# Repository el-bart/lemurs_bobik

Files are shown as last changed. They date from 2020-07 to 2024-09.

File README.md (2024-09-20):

# Lemur's Bobik

project of a toy for a 3-5 year child, that is aimed at learning basic programming skills.
robot has 4 buttons for programming directions and one button to start it.

program is generated by a sequence of buttons pressed (eg. forward, forward, left).
after pressing "start" button, robot begins execution of a given sequence.
its programming is thus similar to Logo programming language, but does not require one to be able to read/write, or spending time in front of the screen.

robot's body is designed to mimic a bit autonomous vacuum cleaner robots, that children know and love. :)

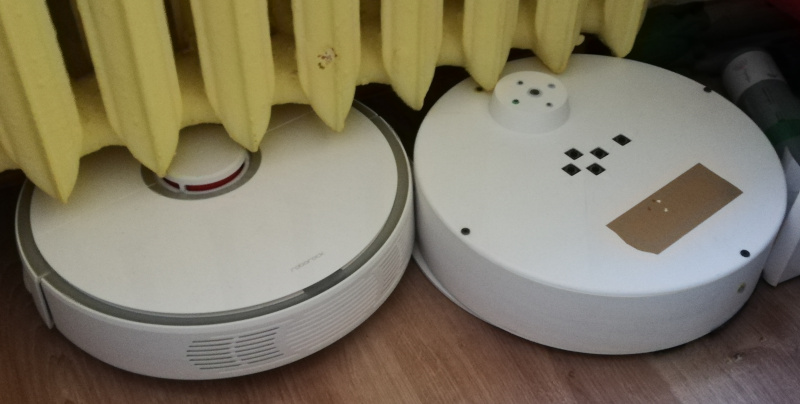
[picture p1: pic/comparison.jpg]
comparison of toy and real robot


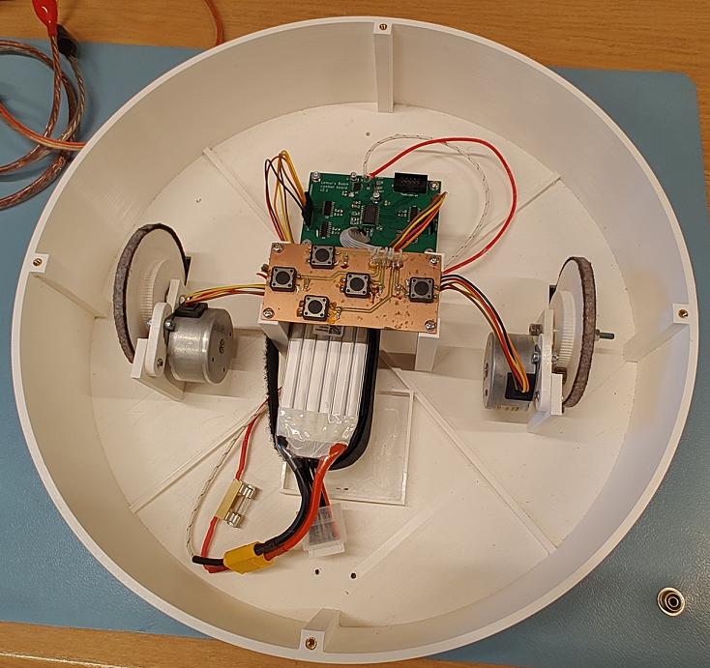
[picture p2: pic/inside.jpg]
robot's interior


## HW parts

* 2x unipolar stepper motors (M42SP-5M - from old desktop printer)
* 12x M3x10 screws
* 12x M3 threaded inserts
* velcro for holding LiPo pack in place (length according to your LiPo size)

## 3D printed parts

`seal` is supposed to be printed in TPU.
after printing, it shall be glued to a `bottom` part with CA glue.
without gluing it will be very hard to put things in place.

all the other elements can be printed in pretty much anything.
my build was just in regular, white PLA.

it's recommend to put some felt under from and rear edges of the bottom part.
it's also worth gluing a thin strip of felt around wheels' external circumference.
this will protect floors from sharp edges and decrease the amount of noise, on flat floors.

while the `seal` is optional, it's highly recommended to silence vibrations.

## electronics

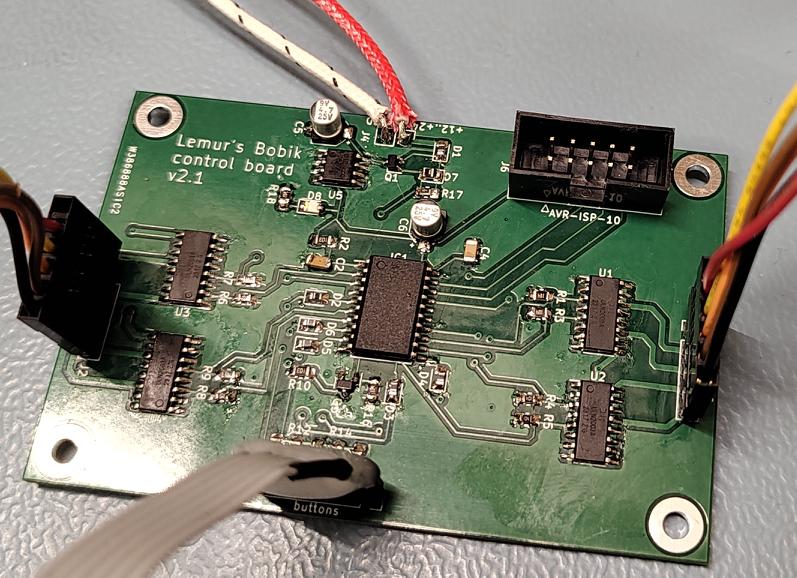
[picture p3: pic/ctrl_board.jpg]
main control board


for electronic components checkout BOM, generated by builds, namely:
```
board/hw/control/build/bom.csv
board/hw/buttons/build/bom.csv
```

## known issues

### engines are hard to mount

screws (especially bottom one) are hard to reach.
in a hindsight whole engine-wheel module should have been reworked.
engines could drive wheels directly, and me mounted with threaded inserts.
this would simplify things a lot, and removed noisy gears altogether.

### missing visual feedback

on top panel there should be more LEDs.
these shall indicate:
* button press recorded (possible with dir)
* powered-on state
* low battery state

### batter status

it should be possible to check batter status w/o opening enclosure and disconnecting it.
currently it's very absorbing and inconvenient.

### OTA

programming via AVR's ISP is annoying and requires disassembly.
as of writing these words (HW v2.1) it also requires unplugging main battery (to be fixed in next HW release).
OTA re-flashing would be an improvement.

### debugability

ATtinty2313 in current setting does not have enough pins to provide any feedback (even LED blinking).
more powerful µC should be used instead, that'd allow for serial (or BTLE) port debugging, to monitor state.
on top of that in-system `gdb` would save time for finding stupid mistakes.
this would greatly simplify finding issues and diagnosing inconveniences, that currently require a lot of fuss and re-flashing.

### need better engines

desktop printer engines used require unusual voltage (here: 24V, 0.35A).
they are also quite weak (here: can easily be stopped with 2 fingers).
more powerful NEMA 17 engines would be far superior choice.
using bipolar steppers would also allow to use off the shelve stepper drivers and provide more torque.

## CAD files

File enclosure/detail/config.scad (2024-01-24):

wall = 4;
cylinder_d = 340;
cylinder_h = 75;
seal_h = 1;

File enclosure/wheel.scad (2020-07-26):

module tooth_(h)
{
  $fs=0.01;
  $fn=0;
  difference()
  {
    union()
    {
      translate([0, 0.4, 0])
        cylinder(r=0.8/2, h=h);
      translate([-0.4, -0.1, 0])
        cube([0.8, 0.5, h]);
    }
    translate([-0.4, -1, 0])
      cube([0.8, 1, h]);
  }
}

module gear_(h)
{
  r=22.1544;
  pi=3.1415926535897932385;
  l=2*pi*r;
  n=l/(0.8*2);
  echo("R=", r);
  echo("N=", n);
  echo("ratio=", n/16);
  cylinder(r=r, h=h, $fn=200);
  for(i=[0:n-1])
    rotate(i*[0, 0, 360/n])
      translate([0, r, 0])
        tooth_(h);
}

module wheel()
{
  h=6;
  difference()
  {
    union()
    {
      cylinder(h=h, r=40, $fs=0.1, $fn=1*360);
      translate([0, 0, h])
        gear_(h);
    }
    cylinder(r=4.3/2, h=2*h+1, $fn=1*360);
  }
}

for(i=[0:1])
  translate(i*[0, 80+5, 0])
    wheel();

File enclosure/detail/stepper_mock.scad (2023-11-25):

module stepper_mock()
{
  cylinder(r=42/2, h=23);
  difference()
  {
    hull()
    {
      for(dx=[-1,1])
        translate([dx*(56.5/2-2*5/2), 0, 23-1])
          cylinder(r=5, h=1);
    }
    for(dx=[-1,1])
      translate([dx*(56.5-2*1.8-2*3.5/2)/2, 0, 23-1-1])
        cylinder(r=3.3/2, h=3);
  }
  translate([0, 0, 23])
  {
    cylinder(r=1, h=18.8);
    translate([0, 0, 18.8-5])
      cylinder(r=9/2, h=5);
  }
}


stepper_mock();

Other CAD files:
enclosure/bottom.scad
enclosure/detail/battery_pack_holder.scad
enclosure/detail/electronics_mocks.scad
enclosure/engine_mount_reg.scad
enclosure/m3d/fn.scad
enclosure/m3d/inner_shell.scad
enclosure/m3d/map.scad
enclosure/m3d/nema17_stepper.scad
enclosure/m3d/outer_shell.scad
enclosure/m3d/rounded_cube.scad
enclosure/m3d/screw_head_hex.scad
enclosure/seal.scad
enclosure/top.scad

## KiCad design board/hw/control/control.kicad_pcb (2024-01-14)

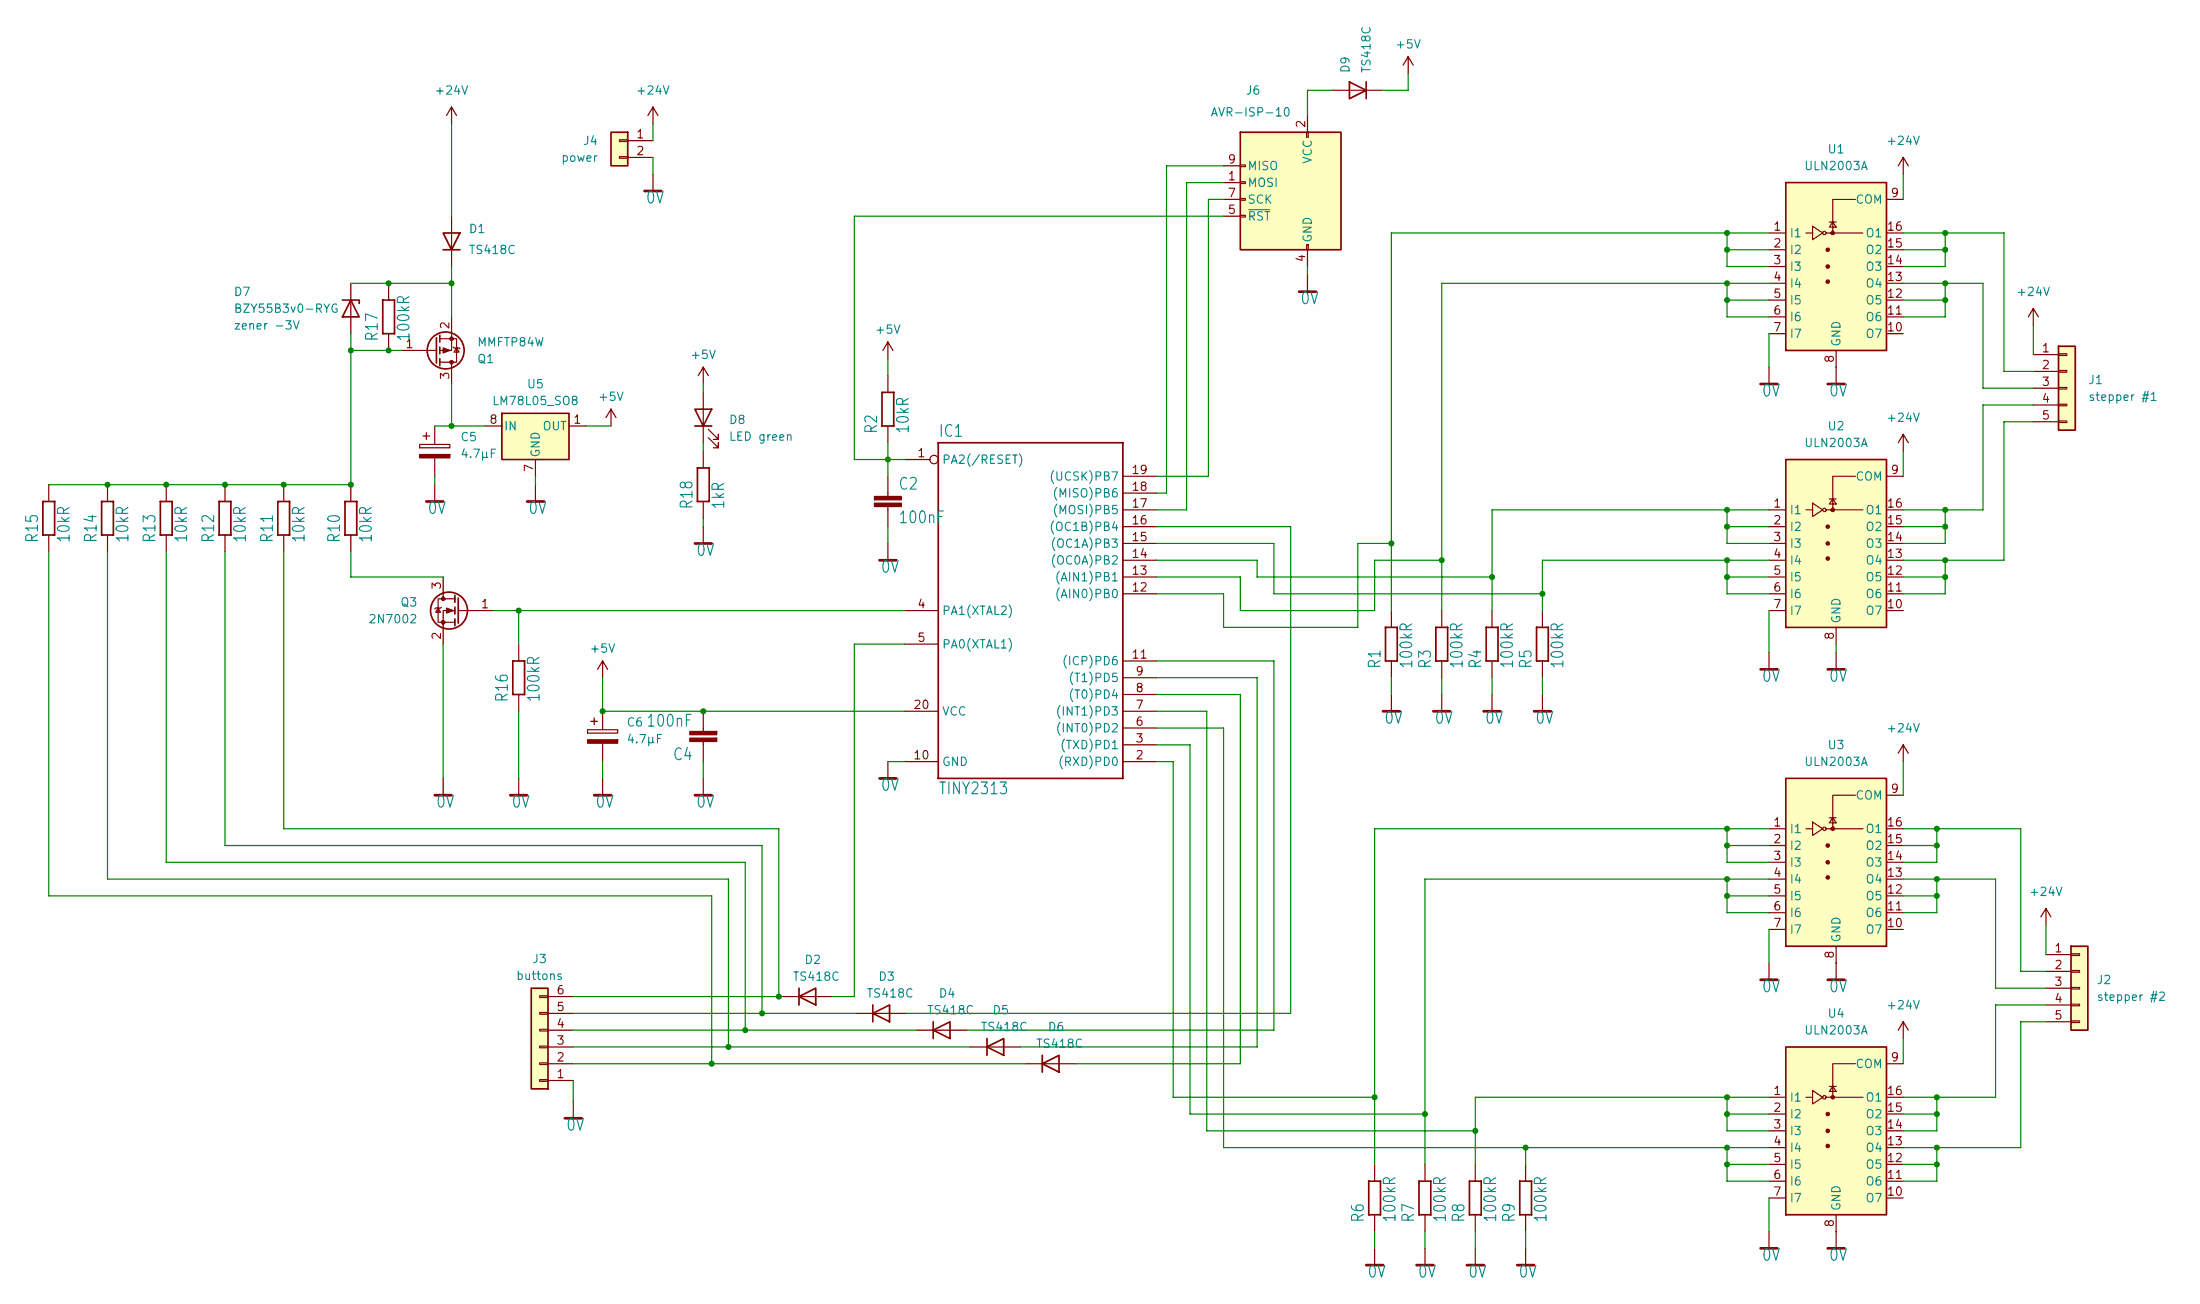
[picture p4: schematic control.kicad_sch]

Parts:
C2, C4: 100nF; C_1206_3216Metric_Pad1.33x1.80mm_HandSolder
C5, C6: 4.7µF; CP_Elec_4x5.8
D1, D2, D3, D4, D5, D6, D9: TS418C; D_0805_2012Metric
D7: BZY55B3v0-RYG; D_0805_2012Metric_Pad1.15x1.40mm_HandSolder
D8: LED green; LED_0805_2012Metric_Pad1.15x1.40mm_HandSolder
IC1: TINY2313; SOIC-20W_7.5x12.8mm_P1.27mm
J1: stepper #1; PinHeader_1x05_P2.54mm_Vertical
J2: stepper #2; PinHeader_1x05_P2.54mm_Vertical
J3: buttons; PinSocket_1x06_P2.54mm_Vertical
J4: power; PinHeader_1x02_P2.54mm_Vertical
J6: AVR-ISP-10; IDC-Header_2x05_P2.54mm_Vertical
Q1: MMFTP84W; SOT-323_SC-70
Q3: 2N7002; SOT-23
R1, R3, R4, R5, R6, R7, R8, R9, R16, R17: 100kR; R_0805_2012Metric_Pad1.20x1.40mm_HandSolder
R2, R10, R11, R12, R13, R14, R15: 10kR; R_0805_2012Metric_Pad1.20x1.40mm_HandSolder
R18: 1kR; R_0805_2012Metric_Pad1.20x1.40mm_HandSolder
U1, U2, U3, U4: ULN2003A; SOIC-16_3.9x9.9mm_P1.27mm
U5: LM78L05_SO8; SOIC-8_3.9x4.9mm_P1.27mm

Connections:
0V: C2.2, C4.1, C5.2, C6.2, IC1.10 (GND), J3.1, J4.2, J6.4 (GND), J6.6 (GND), J6.8 (GND), J6.10 (GND), Q3.2 (S), R1.1, R3.1, R4.1, R5.1, R6.1, R7.1, R8.1, R9.1, R16.1, R18.1, U1.7 (I7), U1.8 (GND), U2.7 (I7), U2.8 (GND), U3.7 (I7), U3.8 (GND), U4.7 (I7), U4.8 (GND), U5.2 (GND), U5.3 (GND), U5.6 (GND), U5.7 (GND)
+5V: C4.2, C6.1, D8.2 (A), D9.1 (K), IC1.20 (VCC), R2.2, U5.1 (OUT)
+24V: D1.2 (A), J1.1, J2.1, J4.1, U1.9 (COM), U2.9 (COM), U3.9 (COM), U4.9 (COM)
unnamed: D1.1 (K), D7.1 (K), Q1.2 (S), R17.2
unnamed: D2.2 (A), IC1.5 (PA0(XTAL1))
unnamed: D2.1 (K), J3.6, R11.1
unnamed: D3.2 (A), IC1.16 ((OC1B)PB4)
unnamed: D3.1 (K), J3.5, R12.1
unnamed: D4.2 (A), IC1.11 ((ICP)PD6)
unnamed: D4.1 (K), J3.4, R13.1
unnamed: D5.2 (A), IC1.9 ((T1)PD5)
unnamed: D5.1 (K), J3.3, R14.1
unnamed: D6.2 (A), IC1.8 ((T0)PD4)
unnamed: D6.1 (K), J3.2, R15.1
unnamed: D7.2 (A), Q1.1 (G), R10.2, R11.2, R12.2, R13.2, R14.2, R15.2, R17.1
unnamed: D8.1 (K), R18.2
unnamed: D9.2 (A), J6.2 (VCC)
unnamed: IC1.12 ((AIN0)PB0), R1.2, U1.1 (I1), U1.2 (I2), U1.3 (I3)
unnamed: IC1.13 ((AIN1)PB1), R3.2, U1.4 (I4), U1.5 (I5), U1.6 (I6)
unnamed: IC1.6 ((INT0)PD2), R9.2, U4.4 (I4), U4.5 (I5), U4.6 (I6)
unnamed: IC1.7 ((INT1)PD3), R8.2, U4.1 (I1), U4.2 (I2), U4.3 (I3)
unnamed: IC1.18 ((MISO)PB6), J6.9 (MISO)
unnamed: IC1.17 ((MOSI)PB5), J6.1 (MOSI)
unnamed: IC1.14 ((OC0A)PB2), R4.2, U2.1 (I1), U2.2 (I2), U2.3 (I3)
unnamed: IC1.15 ((OC1A)PB3), R5.2, U2.4 (I4), U2.5 (I5), U2.6 (I6)
unnamed: IC1.2 ((RXD)PD0), R6.2, U3.1 (I1), U3.2 (I2), U3.3 (I3)
unnamed: IC1.3 ((TXD)PD1), R7.2, U3.4 (I4), U3.5 (I5), U3.6 (I6)
unnamed: IC1.19 ((UCSK)PB7), J6.7 (SCK)
unnamed: IC1.4 (PA1(XTAL2)), Q3.1 (G), R16.2
unnamed: C2.1, IC1.1 (PA2(/RESET)), J6.5 (~RST), R2.1
unnamed: J1.2, U1.14 (O3), U1.15 (O2), U1.16 (O1)
unnamed: J1.3, U1.11 (O6), U1.12 (O5), U1.13 (O4)
unnamed: J1.4, U2.14 (O3), U2.15 (O2), U2.16 (O1)
unnamed: J1.5, U2.11 (O6), U2.12 (O5), U2.13 (O4)
unnamed: J2.2, U3.14 (O3), U3.15 (O2), U3.16 (O1)
unnamed: J2.3, U3.11 (O6), U3.12 (O5), U3.13 (O4)
unnamed: J2.4, U4.14 (O3), U4.15 (O2), U4.16 (O1)
unnamed: J2.5, U4.11 (O6), U4.12 (O5), U4.13 (O4)
unnamed: C5.1, Q1.3 (D), U5.8 (IN)
unnamed: Q3.3 (D), R10.1

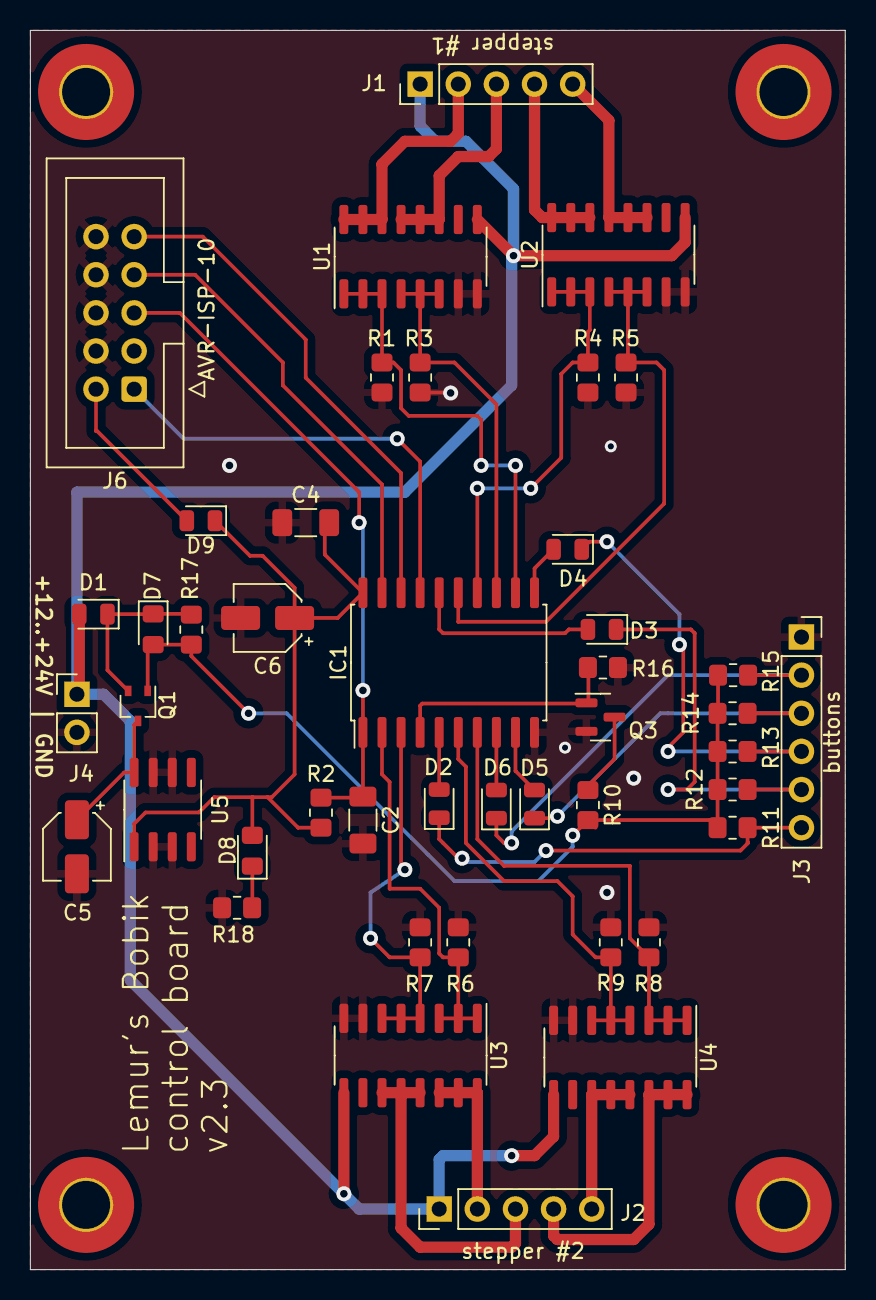
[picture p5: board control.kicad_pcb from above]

Board: 2 copper layers, 54.3 x 82.5 mm, 48 parts (0 on the bottom side), 40 nets.

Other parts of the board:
1, 2, 3, 4: M3; MountingHole_3.2mm_M3_Pad_TopBottom

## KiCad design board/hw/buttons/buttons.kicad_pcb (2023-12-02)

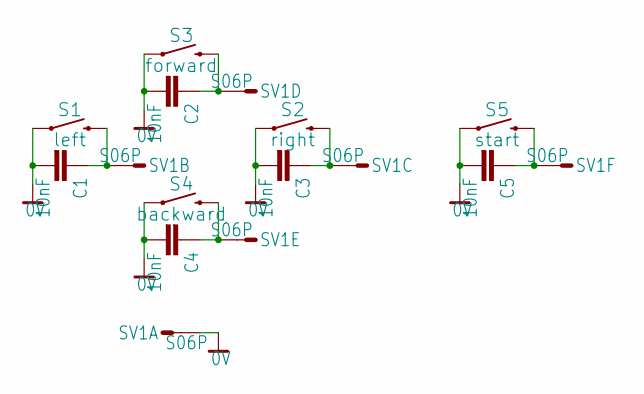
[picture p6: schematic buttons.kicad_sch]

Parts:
C1, C2, C3, C4, C5: 10nF; C0805K
S1: left; TACTILE_SWITCH_SMD_12MM
S2: right; TACTILE_SWITCH_SMD_12MM
S3: forward; TACTILE_SWITCH_SMD_12MM
S4: backward; TACTILE_SWITCH_SMD_12MM
S5: start; TACTILE_SWITCH_SMD_12MM
SV1: S06P

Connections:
0V: C1.2, C2.2, C3.2, C4.2, C5.2, S1.1, S2.1, S3.1, S4.1, S5.1, SV1.1
unnamed: C1.1, S1.3 (2), SV1.2
unnamed: C3.1, S2.3 (2), SV1.3
unnamed: C2.1, S3.3 (2), SV1.4
unnamed: C4.1, S4.3 (2), SV1.5
unnamed: C5.1, S5.3 (2), SV1.6

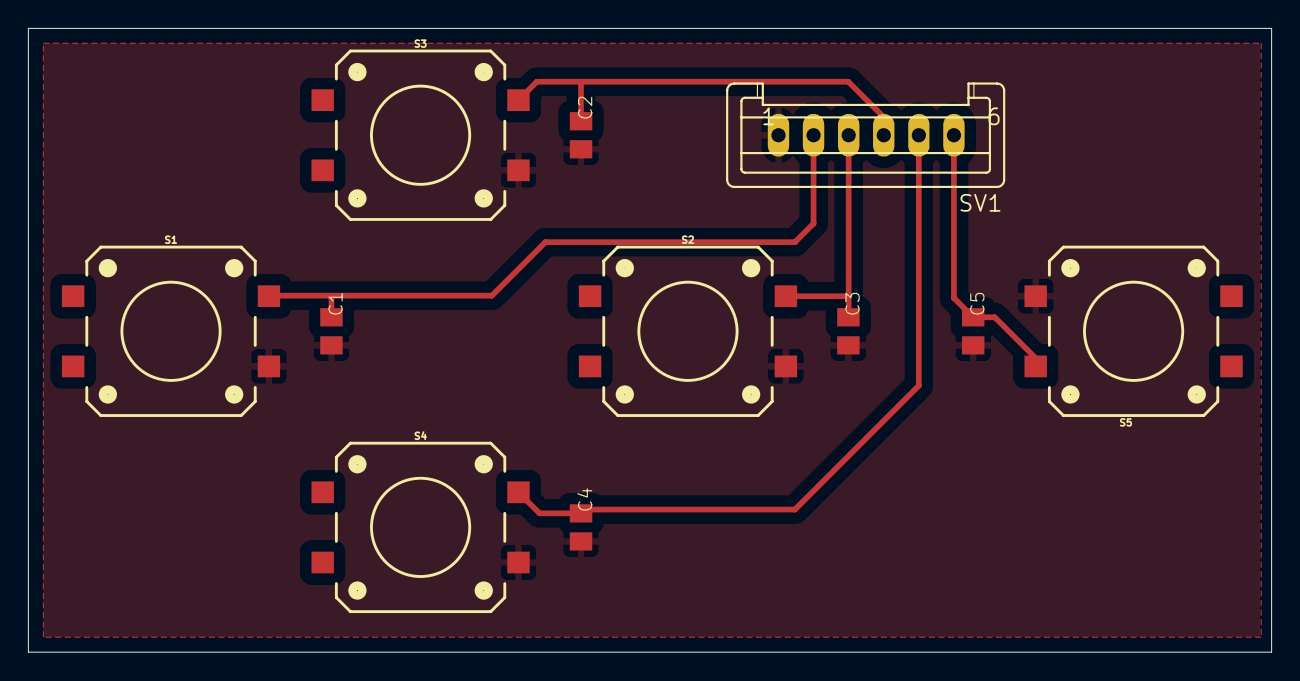
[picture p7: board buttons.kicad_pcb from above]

Board: 2 copper layers, 88.6 x 44.4 mm, 11 parts (0 on the bottom side), 6 nets.

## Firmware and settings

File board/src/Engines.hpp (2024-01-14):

#pragma once
#include "config.hpp"
#include <util/delay.h>

// LEFT  SEQ: PD0 PD2 PD1 PD3
// RIGHT SEQ: PB0 PB2 PB1 PB3
// min  - 15[ms] per step!
// good - 30[ms] per step!

namespace Engines
{

struct PortB
{
  static void init_bits(uint8_t b)   { DDRB |=  b; }
  static void set_bits(uint8_t b)   { PORTB |=  b; }
  static void clear_bits(uint8_t b) { PORTB &= ~b; }
};


struct PortD
{
  static void init_bits(uint8_t b)   { DDRD |=  b; }
  static void set_bits(uint8_t b)   { PORTD |=  b; }
  static void clear_bits(uint8_t b) { PORTD &= ~b; }
};


template<typename Port, uint8_t B0, uint8_t B1, uint8_t B2, uint8_t B3>
struct Generic
{
  Generic() { Port::init_bits( all_bits() ); }
  void off() { Port::clear_bits( all_bits() ); }
  void step_forward() { go_to_pos( next_pos() ); }
  void step_backward() { go_to_pos( prev_pos() ); }

private:
  static auto all_bits() { return B0 | B1 | B2 | B3; }

  void go_to_pos(uint8_t pos)
  {
    off();
    Port::set_bits( pos2bit(pos) );
    pos_ = pos;
  }

  uint8_t pos2bit(uint8_t pos) const
  {
    switch(pos)
    {
      case 0: return B0;
      case 1: return B1;
      case 2: return B2;
      case 3: return B3;
    }
    return 0xFF;    // should never reach here...
  }

  uint8_t next_pos() const
  {
    if(0 < pos_)
      return pos_ - 1;
    return 3;
  }

  uint8_t prev_pos() const
  {
    if(pos_ < 3)
      return pos_ + 1;
    return 0;
  }

  uint8_t pos_{0};
};


using Left  = Generic<PortD, _BV(3), _BV(1), _BV(2), _BV(0)>;
using Right = Generic<PortB, _BV(3), _BV(1), _BV(2), _BV(0)>;

}

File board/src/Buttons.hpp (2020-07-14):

#pragma once
#include "config.hpp"

// BUT_FWD:   PD6
// BUT_BCK:   PB4
// BUT_LEFT:  PD4
// BUT_RIGHT: PD5

// BUT_START: PA0


namespace Buttons
{

inline void init()
{
  DDRA  &= ~_BV(0);
  PORTA |=  _BV(0);

  DDRB  &= ~_BV(4);
  PORTB |=  _BV(4);

  DDRD  &= ~( _BV(4) | _BV(5) | _BV(6) );
  PORTD |=    _BV(4) | _BV(5) | _BV(6);
}


inline bool forward_pressed()  { return not (PIND & _BV(6)); }
inline bool backward_pressed() { return not (PINB & _BV(4)); }
inline bool left_pressed()     { return not (PIND & _BV(4)); }
inline bool right_pressed()    { return not (PIND & _BV(5)); }
inline bool start_pressed()    { return not (PINA & _BV(0)); }

inline bool any_pressed()
{
  return forward_pressed()  ||
         backward_pressed() ||
         left_pressed()     ||
         right_pressed()    ||
         start_pressed();
}

}

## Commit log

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2020-04-20 added some basic prints for elements
    [wheel.scad]
2020-04-20 gear part is a bit more precise with longer teeth + added rod wole in the center
    [wheel.scad]
2020-04-20 decreased drive rod hole + added 2 elements on 1 print
    [wheel.scad]
2020-04-21 renamed body to enclosure (more accurate)
    [wheel.scad]
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2020-04-21 moved sources next to hardware schematics + added draft of a control board (schematics for now)
    [control.brd, control.sch]
2020-04-21 buttons board is ready
    [buttons.brd, buttons.sch]
2020-04-21 removed capacitors for buttons - these are already covered by the external board
    [control.brd, control.sch]
2020-04-21 single-layer routing completed (yay)
    [control.brd, control.sch]
2020-04-21 moved KANDA connector in order to simplifiy and reduce board a bit
    [control.brd]
2020-04-22 decreased board size to cover only copper part
    [buttons.brd]
2020-04-23 added 10nF to button boards capacitors
    [buttons.brd, buttons.sch]
2020-04-23 reorganized labels, so that these fit on the board
    [control.brd]
2020-04-23 more labels moved not to collide
    [control.brd]
2020-04-23 moved everything to a bottom layer
    [control.brd]
2020-04-23 added note on the board, with version
    [buttons.brd]
2020-04-23 added board name to a caption
    [control.brd]
2020-04-24 placeholders for next elements
    [bottom.scad, distance.scad, top.scad]
2020-04-24 main hull + wheel axis mounts
    [bottom.scad]
2020-04-24 wheels hole is now bigger and wider
    [bottom.scad]
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2020-04-25 added missing power supply connector
    [control.brd, control.sch]
2020-04-28 element that can regulat engine mount
    [engine_mount_reg.scad]
2020-04-28 2x engine mount printed at once
    [engine_mount_reg.scad]
2020-04-29 fixed axis diameters/radiuses
    [engine_mount_reg.scad]
2020-04-29 added battery pack mount
    [bottom.scad]
2020-04-29 increased height of bobik, so that wheels squeeze in
    [bottom.scad]
2020-04-29 added buttons and control board + moved battery pack closer to the center
    [bottom.scad]
2020-04-29 electronic mocks added to VCS
    [electronics_mocks.scad]
2020-04-29 electronics mocks are now printable
    [electronics_mocks.scad]
2020-04-29 added screw holders for top part + bottom balancing elements
    [bottom.scad]
2020-04-29 added reinforcements on the bottom, for better structural rigidity
    [bottom.scad]
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2020-04-30 back to 102% extrusion - it is ok. the unstucking problem was solved with dimafix
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2020-07-09 added some test code for buttons - these will need a bit more extra work in HW (pull-ups missing)
    [main.cpp]
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2020-07-10 added missing pull-up 100k Rs for all buttons
    [control.brd, control.sch]
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2020-07-15 fixed forward/backward sequences mix
    [Engines.hpp]
2020-07-16 external gears generation module
    [gears.scad]
2020-07-16 moved to gear ratio 15:20 (i.e. 0.75), for improved speed
    [wheel.scad]
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2020-07-16 commented out test gear
    [gears.scad]
2020-07-17 removed unused placeholder file
    [distance.scad]
2020-07-17 restored original test example parameters
    [gears.scad]
2020-07-17 decreased number of teeth in gears, so that they are smaller and can fit into an existing frame
    [wheel.scad]
2020-07-17 scaled the hole so that it fits the actual wheel
    [wheel.scad]
2020-07-18 added wait for all buttons realeased before starting programming + shorter wait for any pressed state
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2020-07-18 decreased ratio to 20:9 (~2.2)
    [wheel.scad]
2020-07-18 moving back to original wheel design, just with a ratio around 2.7 instead of 5.4
    [gears.scad, wheel.scad]
2020-07-19 moved hole a bit to front, so that smaller gear on the wheel can be compenstated
    [engine_mount_reg.scad]
2020-07-20 restored back wheels from before making gear-ratio changes. steppers used are too weak to handle smaller ratios, aspecially on a non-flat surfaces
    [engine_mount_reg.scad, wheel.scad]
2020-07-20 removed TODO for decreased gear ratio - did not work out
2020-07-26 increased resolution on certain round elements
    [bottom.scad, wheel.scad]
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2020-07-26 added map cap block, with rounded edges
    [top.scad]
2020-07-26 added placeholder for cap holes
    [top.scad]
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2020-08-03 moved capacitor hole closed to the button (where it should be) + fixed main part's resolution
    [top.scad]
2020-08-03 replaced hardcoded value with a math to get it, so that it is more visible where it comes from
    [top.scad]
2020-08-03 buttons are now standing out, not being cut-in
    [top.scad]
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2023-11-25 updated SDK an set to build in PLA/precise
    [fn.scad, inner_shell.scad, map.scad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]
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2023-11-25 increased top screw hole diameter, to make a loose fit for M3 bolt
    [top.scad]
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2023-11-25 removing old Eagle CAD project of the ctrl board
    [control.brd, control.sch]
2023-11-25 holes are no longer highlighted
    [stepper_mock.scad]
2023-11-25 moved old stepper motor mock in place of NEMA 17
    [bottom.scad, stepper_mock.scad]
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2023-11-25 removed holes for balancing elements - sticking in felt works well enough
    [bottom.scad]
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2023-12-02 moved most elements from Eagle to KiCad libraries
    [control.kicad_pcb, control.kicad_sch]
2023-12-02 removed unused elements and added proper AVR-ISP-10 conector
    [control.kicad_pcb, control.kicad_sch]
2023-12-02 assigned correct sizes of elements + some draft positioning; still need to add power management cirtcuitry
    [control.kicad_pcb, control.kicad_sch]
2023-12-26 added p-mosfet and zerenrs for power ctrl via buttons, too
    [control.kicad_pcb, control.kicad_sch]
2023-12-26 PCB routing mostly done - DRC is WIP
    [control.kicad_pcb]
2023-12-26 fixed all DRC errors and most warnings
    [control.kicad_pcb]
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2023-12-26 re-enabled all warnings and fixed siklscreen overlapping items
    [control.kicad_pcb]
2023-12-26 'stepper #1' silk rotated correctly
    [control.kicad_pcb]
2023-12-26 vias for screws moved to MountingHole, so that it's clearly visible in 3D preview
    [control.kicad_pcb]
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2023-12-26 added mount holes instead of vias + associated mess
    [control.kicad_pcb, control.kicad_sch]
2023-12-26 mountholes adjusted to better match existing 3D mount points on the model
    [control.kicad_pcb]
2023-12-26 fixed track widths for power lines to steppers
    [control.kicad_pcb]
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2023-12-26 replaced P-MOSFET with N-MOSFET to maintain power-on state
    [control.kicad_pcb, control.kicad_sch]
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2024-01-14 engines directions are swaped
    [Engines.hpp]
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2024-01-14 C2 and C4 are not 1206 as they should
    [control.kicad_pcb, control.kicad_sch]
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2024-01-14 batter slot is now for velcro + LiPo pack
    [battery_pack_holder.scad, bottom.scad]
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2024-01-14 fixed the issue where wake-up button press was not added to program sequence
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2024-01-14 added diade so that AVR's ISP can optionaly power the board, but board power will not damage the programmer
    [control.kicad_pcb, control.kicad_sch]
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2024-01-24 aggresive usage of m3d's fn() for faster previews
    [bottom.scad, top.scad]
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2024-01-24 renamed main module to align with file name + removed bottom visuzalitaion
    [top.scad]
2024-01-24 added visualizatrion of both top() and seal() in preview
    [bottom.scad]
2024-01-24 added preview of top and seal by default
    [bottom.scad]
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2024-01-24 pcb_control.stl is now to be copied from the control board's build
    [pcb_control.stl]
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2024-09-20 fixed a couple typos
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
